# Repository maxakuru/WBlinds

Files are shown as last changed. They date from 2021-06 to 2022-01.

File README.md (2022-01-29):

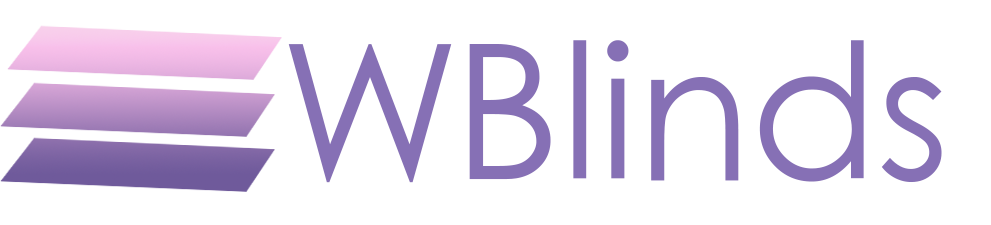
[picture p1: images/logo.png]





Build Wifi-connected smart blinds using ESP32 and off-the-shelf components for <$50.

🌟 Including...
* [HTTP/REST API](#http)
* [MQTT API](#mqtt) & client
* Native [Homekit](#homekit) integration
* Halts on home detection
* [Web UI](#web-ui) for controlling/configuring

## Table of Contents
<!--ts-->
   * [Setup](#setup)
      * [Hardware](#hardware)
      * [Circuit](#circuit)
      * [Software](#software)
   * [APIs](#apis)
   * [Web UI](#web-ui)
   * [Configuration](#configuration)
   * [Development](#development)
      * [Custom Integrations](#custom-integrations)
   * [Appendix](#appendix)
      * [Other Files](#other-files)
      * [Choosing a Motor](#choosing-a-motor)
<!--te-->

<h2 id="setup">✏️ Setup</h2>

### Hardware
These are some suggestions for hardware to use. The first link in each row is the product I used for the prototype. All links are non-affiliate and can be found elsewhere if you look around. Prices are estimates including shipping at the time I purchased and may have changed since then; I suggest searching around if so.

<table>
  <tbody>
    <tr>
      <th>Part ~~~~~~~~</th>
      <th>Purchase Links ~~~~~~~~~~~~~~~~~~~~~~~~~~~~</th>
      <th>Notes <br> ~~~~~~~~~~~~~~~~~~~~~~~~~~~~</th>
    </tr>
    <tr>
      <td>ESP32</td>
      <td>
        • <a href=https://www.aliexpress.com/item/1005001648850998.html>32S Devkit "V1" (AliExpress, $4)</a><br>
        • <a href=https://www.mouser.com/ProductDetail/Espressif-Systems/ESP32-S2-DevKitM-1?qs=DPoM0jnrROXzO8seOHN%252BOQ%3D%3D>32S Devkit M1 (Mouser, $8)</a><br>
        • <a href=https://www.amazon.com/HiLetgo-ESP-WROOM-32-Development-Microcontroller-Integrated/dp/B0718T232Z>NodeMCU-32 (Amazon, $11)</a>
      </td>
      <td>Circuit below wass using the first link. Pin assignments may vary between boards, often the same pins but more/less extra pins, or power pins are in different places. Be sure to check the pinout.</td>
    </tr>
    <tr>
      <td>Stepper Driver</td>
      <td>
        • <a href=https://www.aliexpress.com/item/1005001374747956.html>A4988 (AliExpress, $2)</a><br>
        • <a href=https://www.pololu.com/product/1182>A4988 (Polulu, $6)</a><br>
        • <a href=https://www.amazon.com/Aokin-StepStick-Stepper-Driver-Printer/dp/B07JV835SW>5x A4988 (Amazon, $8)</a>
      </td>
      <td>Other drivers would work too, currently only A4988 is tested (using <a href=https://github.com/gin66/FastAccelStepper>FastAccelStepper</a>). <br><br> Be sure to <a href=https://youtu.be/89BHS9hfSUk>set the current limit</a> before attaching your motor.</td>
    </tr>
    <tr>
      <td>Stepper Motor</td>
      <td>
        • <a href=https://www.aliexpress.com/item/1005002191787745.html>1.5A 45Ncm (AliExpress, $18)</a><br>
         <a href="https://www.omc-stepperonline.com/nema-17-bipolar-42ncm-59-49oz-in-1-5a-42x42x39mm-4-wires-w-1m-cable-and-connector.html">1.5A 42Ncm (StepperOnline, $5 at time of writing)</a>
        • <a href=https://www.pololu.com/product/2267>1.7A 36Ncm (Polulu, $18)</a><br>
        • <a href=https://www.amazon.com/Twotrees-Stepper-17HS4401-Connector-Printer/dp/B07THK76QQ>1.5A 42Ncm (Amazon, $10)</a>
      </td>
      <td>This may be over/underpowered for your needs, depending on the weight of the blinds. <br> <br> See <a href="#choosing-a-motor">choosing a motor</a>. <br> <br> 
      Note: The newest 3d designs use a worm gear with a 30:1 reductions so a much smaller motor will work, but the movement speed is greatly reduced with that design.</td>
    </tr>
    <tr>
      <td>3.3V Step-down Regulator</td>
      <td>
        • <a href=https://www.aliexpress.com/item/4000714041437.html>5-40V to 3.3V (AliExpress, $2)</a><br>
        • <a href=https://www.pololu.com/category/209/d24v5fx-step-down-voltage-regulators>D24V5Fx (Polulu, $5)</a><br>
        • <a href=https://www.amazon.com/Anmbest-AMS1117-3-3-4-75V-12V-Voltage-Regulator/dp/B07CP4P5XJ>10x 5-12V to 3.3v (Amazon, $9)</a>
      </td>
      <td>Circuit below is using the one from AliExpress.  Others may have different number of pins or pin orders, so check the pinout before wiring.</td>
    </tr>
    <tr>
      <td>Power supply</td>
      <td>
        • <a href=https://www.aliexpress.com/item/1005001555277278.html>24V 5A (AliExpress, $13)</a><br>
        • <a href=https://www.pololu.com/product/1468>12V 5A (Polulu, $19)</a><br>
        • <a href=https://www.amazon.com/Converter-100-220V-Transformer-5-5x2-1mm-Accessories/dp/B08C594VNP>12V 5A (Amazon, $10)</a>
      </td>
      <td>You can (and probably want to) use a voltage over the motor's rating.  That's fine, you just need to stay below it's rated current. <br> <br>  The current needed depends on motor rating and how many blinds you'll be moving simultaneously with the same power supply.</td>
    </tr>
    <tr>
      <td>DC barrel jack</td>
      <td>
        • <a href=https://www.aliexpress.com/item/4000215113209.html>5.5mm x 2.1mm (AliExpress, $3)</a><br>
      </td>
      <td></td>
    </tr>
    <tr>
      <td>Microswitch</td>
      <td>
        • <a href=https://www.aliexpress.com/item/1926553469.html>5x (AliExpress, $2)</a><br>
        • <a href=https://www.pololu.com/product/1402>1x (Polulu, $1)</a><br>
        • <a href=https://www.amazon.com/Antrader-KW4-3Z-3-Micro-Switch-Switches/dp/B07GDD9PJL>6x (Amazon, $6)</a>
      </td>
      <td>Optional, used as a limit switch for the "fully open" position.  Any switch could work here.</td>
    </tr>
    <tr>
      <td>Blinds</td>
      <td>
        • <a href="https://www.ikea.com/us/en/p/hoppvals-room-darkening-cellular-blind-gray-20386440">HOPPVALS (IKEA, $20-45)</a><br>
        • <a href="https://www.ikea.com/us/en/p/trippevals-black-out-cellular-blind-light-gray-00445006/">TRIPPEVALS (IKEA, $40-60)</a>
      </td>
      <td>My builds use cellular shades from IKEA, modified to wrap the cord around a 3D printed axis, instead of the retail spring mechanism. <br><br>  Any blinds that can be moved by wrapping a cord around an axis could easily be adapted.  Most cordless blinds could be used with some modifications. Roller blinds would be the easiest in most cases.</td>
    </tr>
  </tbody>
</table>

### Circuit
Schematic files are located in the `pcb/` directory. Currently there is a devkit that can be fabricated that fits header pins and will use the following components. Check the parts list carefully, only the first item in each section will fit, since they are what I ordered, but other parts may not. The gerber output is a 2 layer board created with [JLCPCB](https://jlcpcb.com/)'s CAM generator.
- 30 pin ESP32 devkit
- 3 pin buck converter (middle pin GND)
- 3 pin DC barrel jack

You'll also want some pin headers to solder on, both male and female. The parts are throughhole and the gerber has drill holes so you can skip them if you'd like, but I'd recommend at least making the A4988 removable in case you pop one.

#### Schematic
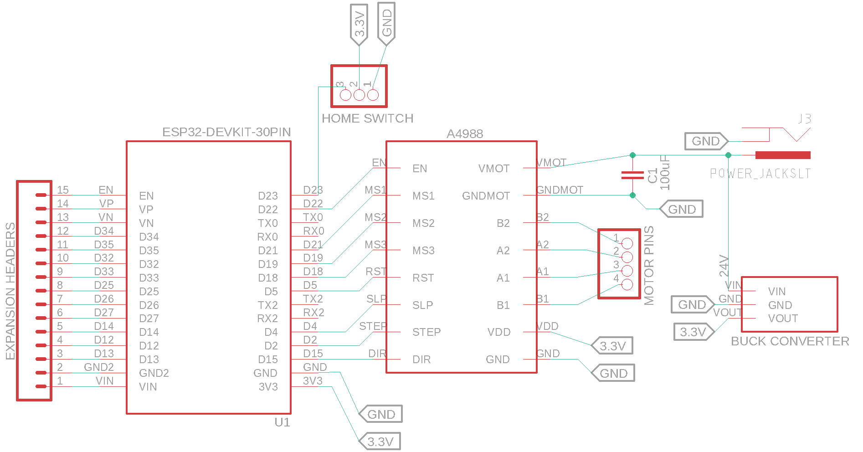
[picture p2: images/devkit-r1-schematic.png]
schematic


#### Devkit
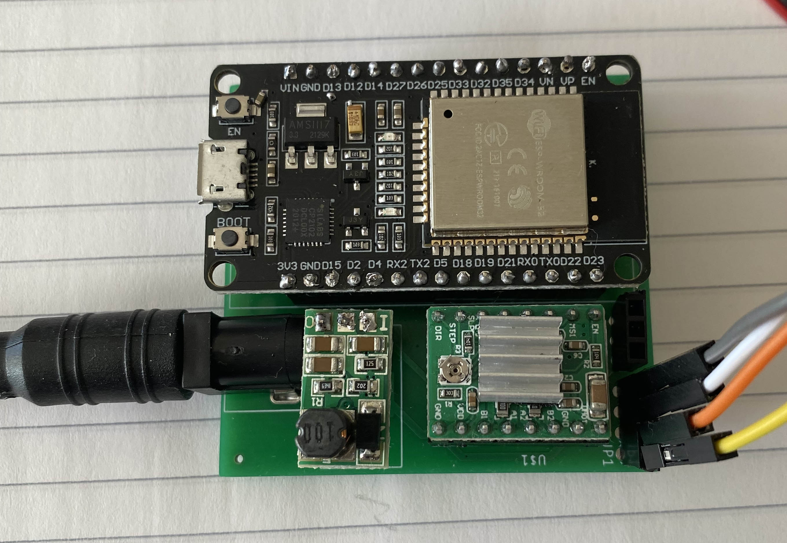
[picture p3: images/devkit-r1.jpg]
devkit


* **Remember to [adjust the current limit](https://youtu.be/89BHS9hfSUk) of the A4988 BEFORE connecting it to the circuit** -- keep the magic smoke inside.
* The pins can be set via the [web UI](#settings), feel free to use different ones.
* Be sure not to apply 12/24V to your ESP or `Vc` (or VDD) of the driver IC. It only goes to `Vm` to power the motor, everything else can use 3.3v.
* A4988's `RST` and `SLP` can be connected to each other if you don't care about the ability to sleep the motor.

### 3D Parts
Included in the `/3d` directory are 2 revisions of printable designs for WBlinds, crafted specifically for Ikea HOPPVALS. The same 2 mechanisms could be reworked for any other blinds. `r1` has the added benefit of a worm gear mechanism, so power doesn't need to be constantly applied to keep the blinds in place, even with heavy materials.

#### Revision 1
These are screenshots of the design to give you an idea of how parts fit together. It may be useful to put a damper ([Amazon](https://www.amazon.com/Rubber-Stepper-Vibration-Damper-Screws/dp/B07415B39B) | [AliExpress](https://www.aliexpress.com/item/4000058411445.html)) between the bracket and the stepper to cut down on vibration & noise.

**Default**

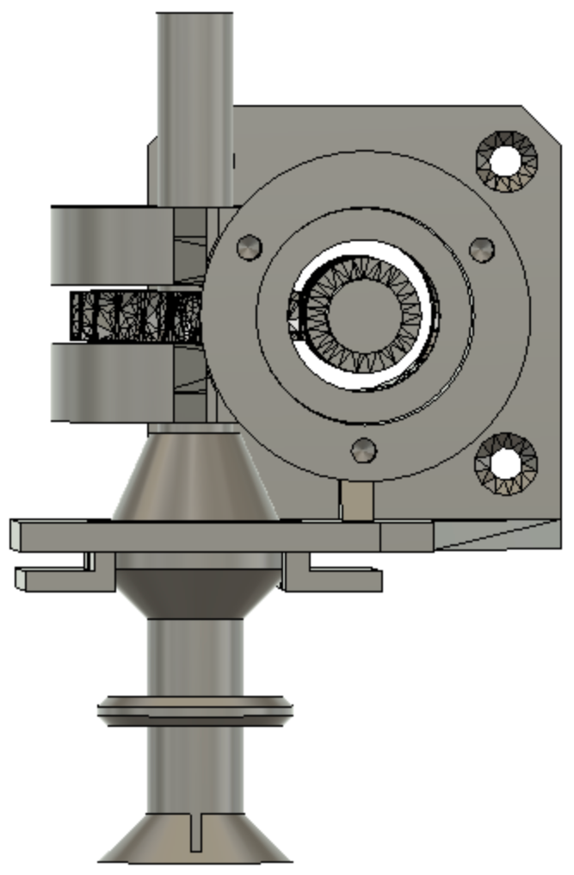
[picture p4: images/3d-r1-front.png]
r1-front
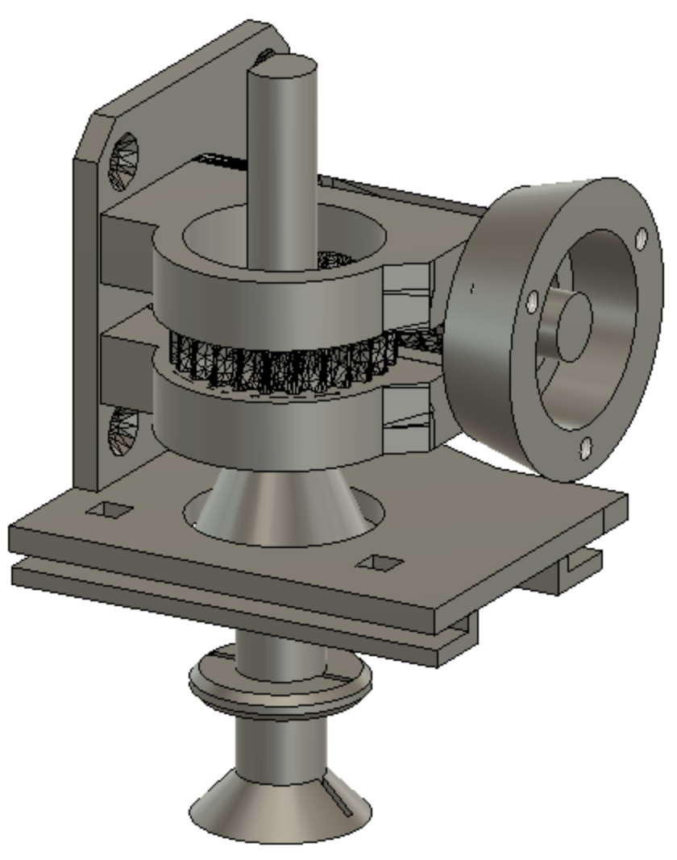
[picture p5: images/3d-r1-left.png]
r1-left
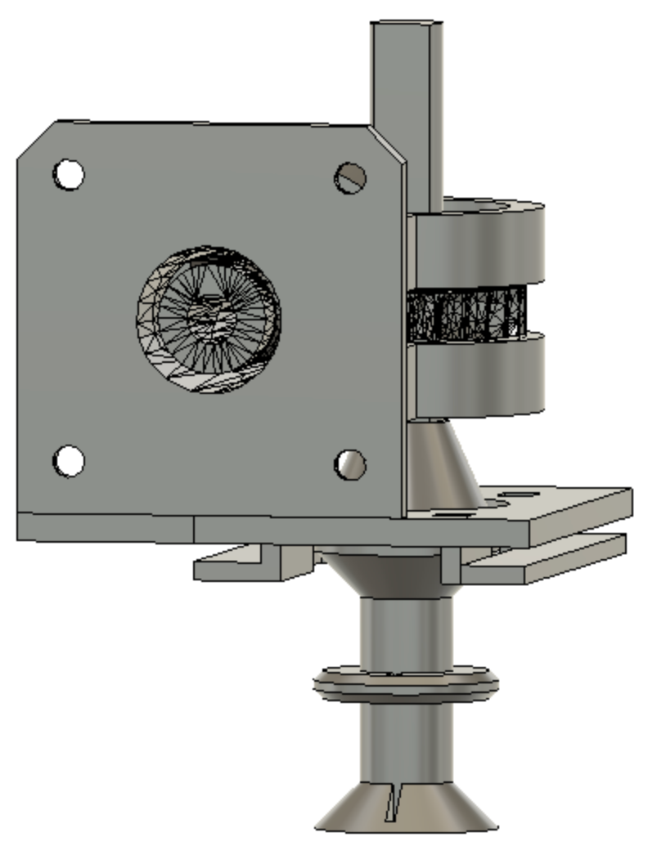
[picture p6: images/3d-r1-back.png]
r1-back
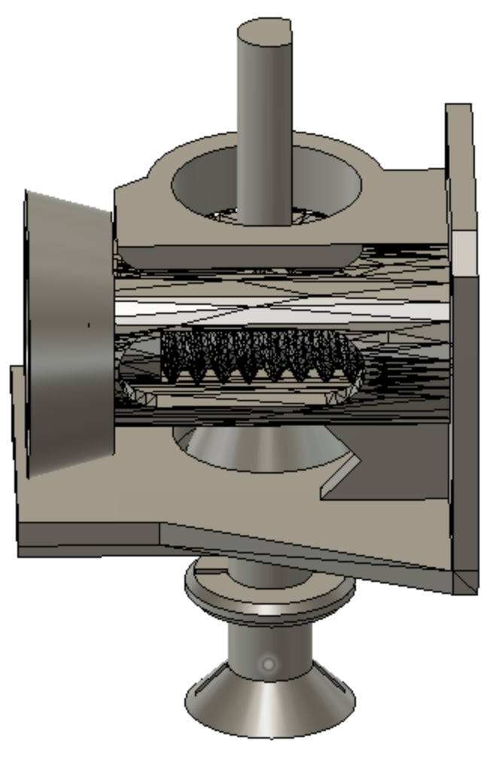
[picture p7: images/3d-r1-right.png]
r1-right


> The `3d/r1/cam/` contains an experimental (and not great) barrel cam mechanism to guide the string along an alternating path around the center spool, functionally similar to what a fishing reel does with a string guide. This can be sticky with 3D-printed parts, and with a good placement of `string-guide.stl`s, it isn't necessary to keep the spooling even.

**With optional cam exposed**

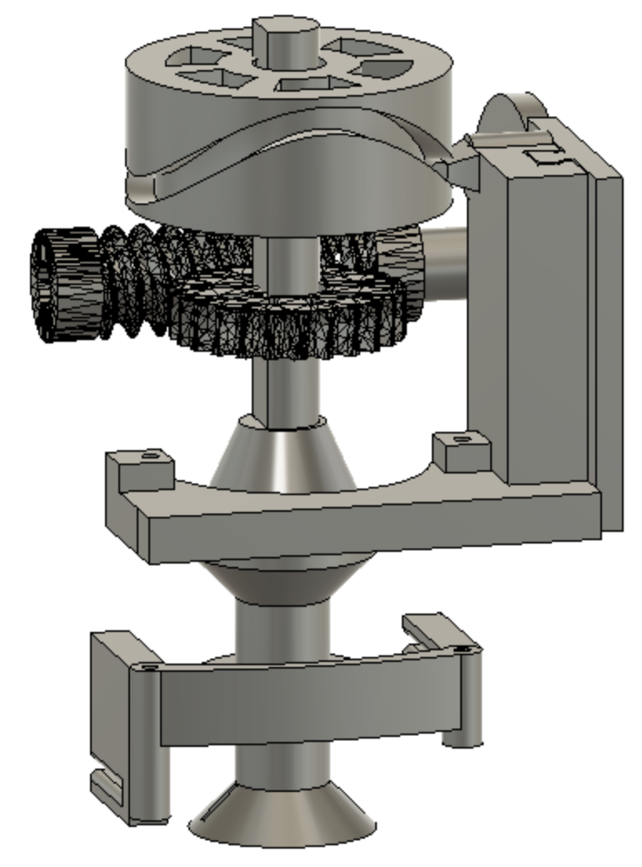
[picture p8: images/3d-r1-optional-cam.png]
r1-with-cam


### Software
1. Connect ESP32 to your computer via USB
2. `git clone https://github.com/maxakuru/WBlinds.git`
3. `cd WBlinds && yarn`
4. `yarn build:cpp`
5. `yarn flash`
6. On first boot an access point will be started, connect to it:
    * SSID: `WBlinds-XXXXXX`
    * Default password: `Wbl1nds-1337`
7. After connecting, a webpage should open to configure settings. If not, go to http://4.3.2.1/settings?tab=gen
8. Configure SSID, password, pins, etc. and tap "SAVE"
9. You will be disconnected from the AP. Find the IP address of the device on your network and enter it in your browser.
> Steps 3-5 assume you have PlatformIO, Node.js, and Yarn installed. You can also flash without Node/Yarn by using the [PlatformIO VSCode Plugin](#tools). You can also use the [scripts](#scripts) to do other stuff.

<h2 id="apis">🔌 APIs</h2>

These APIs are in flux!

### HTTP
```js
PUT <host:port>/api/state
// All fields optional
{ 
    "tPos": 50, //[0-100] (target position %, starts move)
    "pos": 50, // [0-100] (current position %)
    "accel": 99999, // [0-UINT32_MAX] (steps/s/s)
    "speed": 1000, // [0-something reasonable] (Hz)
}
```
```js
GET <host:port>/api/state
// 200
{ 
    "tPos": 50,
    "pos": 50,
    "accel": 99999,
    "speed": 1000
}
```

```js
POST <host:port> 
{ 
    "op": "up" | "down" | "stop" | "sleep"
}
```

```js
PUT <host:port>/api/settings
// All fields optional
// NOTE: data is sent in body as JSON. If that isn't acceptable for your use, set sensitive fields at compile time.
{ 
    gen: { 
        deviceName: "WBlinds", 
        mdnsName: "WBlinds", 
        emitSync: true,
        ssid: "My Network",
        pass: "supersecurepassword"
    },
    hw: {
        pStep: 19,
        pDir: 18,
        pEn: 23,
        pSleep: 21,
        pReset: 3,
        pMs1: 1,
        pMs2: 5,
        pMs3: 17,
        pHome: 4,
        cLen: 1650,
        cDia: 0.1,
        axDia: 15,
        stepsPerRev: 200,
        res: 16,
    },
    mqtt: {
        enabled: true,
        host: "192.168.1.99",
        port: 1883,
        topic: "WBlinds",
        user: "max",
        pass: "mysupersecurepassword"
    }
}
```
```js
GET <host:port>/api/settings
{ 
    gen: { 
        deviceName: "WBlinds", 
        mdnsName: "WBlinds",
        ssid: "Some SSID",
        mac: "abcdef123456",
        emitSync: true
    },
    hw: {
        pStep: 19,
        ...
        res: 16
    },
    mqtt: {
        enabled: true,
        host: "192.168.1.99",
        port: 1883,
        topic: "WBlinds",
        user: "max"
    }
}
```

```js
POST <host:port>/api/restore
// 202, ESP resets once completed
// This wipes Homekit config & state files
```

### MQTT
WBlinds subscribes to a wildcard based on the topic provided.
For example, a topic name `blinds/living_room` will subscribe to `blinds/living_room/#`.

The topic defines a number of actions without any payload, for example:
```sh
topic="blinds/living_room/up"
```
```sh
topic="blinds/living_room/down"
```
```sh
topic="blinds/living_room/stop"
```
```sh
topic="blinds/living_room/sleep"
```

Some topics can specify additional data:
```sh
topic="blinds/living_room/move"
body="{\"pos\":50,\"speed\":1000,\"accel\":1000}"
```
Where `pos` is %, `speed` is Hz, and `accel` is steps/s^2.

### Homekit
Native Homekit integration allows the ESP32 to be detected as a device without a bridge/emulator. This mode requires percentage-based position values, so it's important to calibrate the settings first.

The default Homekit pin is `111-22-333`, and it will be correctly identified as a "window covering".

<h2 id="web-ui">💻 Web UI</h2>

### Home
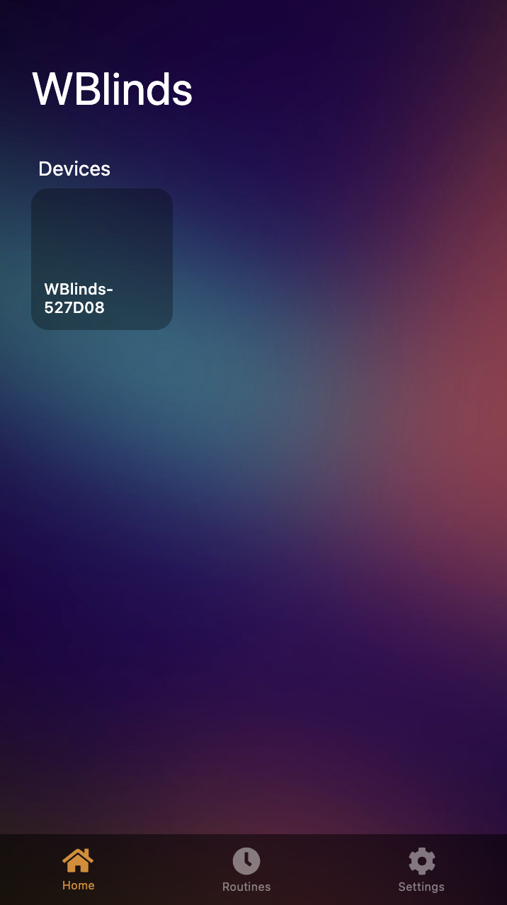
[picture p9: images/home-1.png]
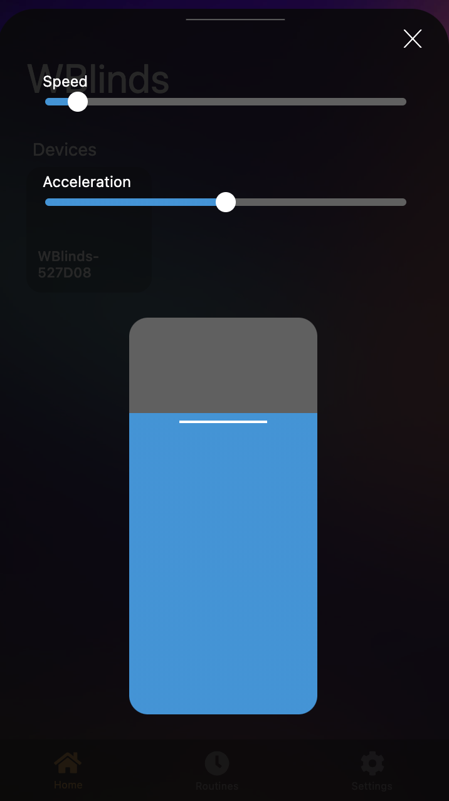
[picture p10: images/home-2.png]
 

### Settings
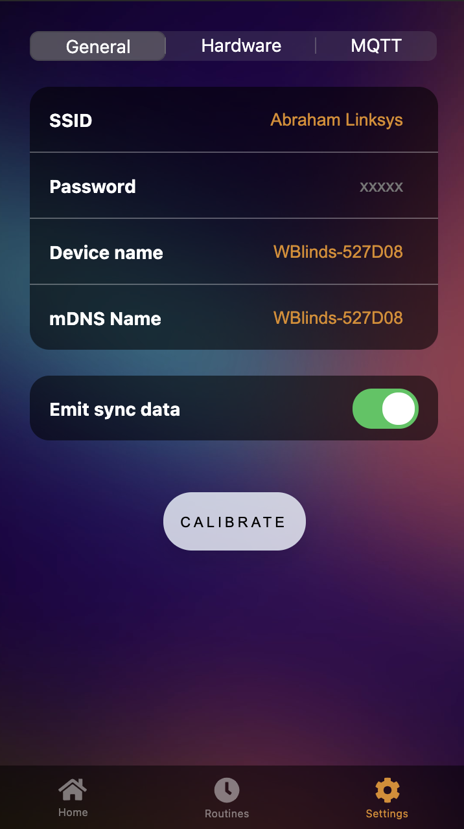
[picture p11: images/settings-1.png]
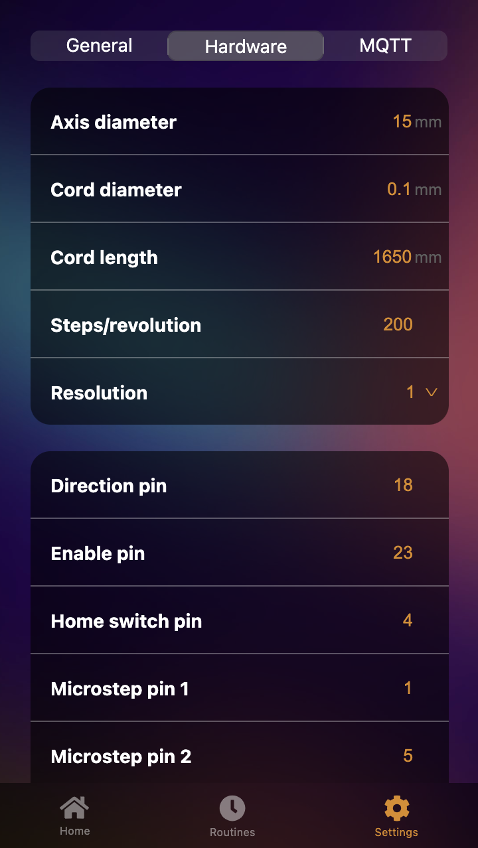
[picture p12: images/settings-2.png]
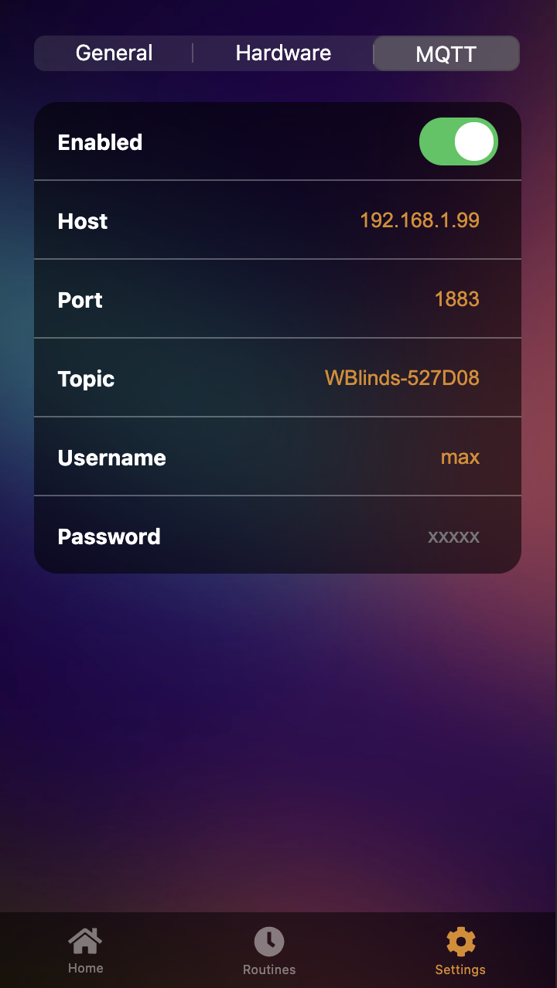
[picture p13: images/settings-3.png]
  

<h2 id="configuration">🔧 Configuration</h2>

There is a `Calibrate` button at `$HOST/settings?tab=gen` that will guide you through a 2 step calibration to find the correct bottom and top positions for the blinds on first setup. These settings will be persisted across power cycles and flashes of new firmwares, as long as you use the same partition.

### Default Pins
| Pin | Use | Description
| --- | --- | ---|
| `17`  | pDir | Controls direction (optional) |
| `5`  | pStep | Controls steps via PWM with A4988 (required) |
| `18`  | pSlp | Allows putting motor to sleep to save most power possible. (optional) |
| `23`  | pEn | Allows enabling/disabling motor with A4988. By default the motor is disabled and enabled between uses which lowers power consumption. (optional)
| `19` | pRst | Reset pin (optional)
| `1` | pMs1 | Microstep resolution pin 1, using microsteps can decrease sound (optional)
| `3` | pMs2 | Microstep resolution pin 2 (optional)
| `21` | pMs3 | Microstep resolution pin 3 (optional)
| `4` | pHomeSw | Home trigger switch, recommended as a way to hard stop when the blinds reach the fully contracted position to avoid damaging hardware when steps are skipped or malfunctions. (optional)

<h2 id="development">📝 Development</h2>

There are 2 projects that make up this repo: the C++ ESP controller and a TypeScript-based web UI. The web UI is transpiled to Javascript, inlined into HTML, then gzipped/chunked into header files with a script. All generated header files as well as transpiled JS is included in the repo, so no additional build steps are needed.

### Scripts
These can be run with `npm` or `yarn`, I'm currently using yarn. None of these are required to build and flash the ESP bin, as mentioned above all the files are checked into git, so you can compile the C part however you like.

However, these scripts are used for pre-commit hooks, so if you want to contribute you'll need Node.js.

#### UI
Build web UI in development/watch mode (outputs to `public/`):
```sh
yarn dev
```

Build web UI minified (outputs to `public/`, also runs `build:uih` afterwards):
```sh
yarn build:ui
```

Only generate header files from `public/`:
```sh
yarn build:uih
```

#### ESP
The following scripts depend on PlatformIO, and can be replaced with the toolbar quick actions in VSCode if you prefer.

Compile C++ (assumes *nix machine right now):
```sh
yarn build:cpp
```

Build & flash using pio:
```sh
yarn flash
```

Flash over-the-air (requires an initial flash while plugged in and WiFi connection established through settings):
```sh
yarn flash:ota $IP_OR_HOSTNAME
```

#### Both
You can combine all build scripts with:
```sh
yarn build
```

### Tools
I recommend using VSCode to build/flash. Eventually I plan to cut releases of precompiled binary that can be flashed directly, but for the time being you'll need to pull the code and compile it yourself. That is made very simple by the wonderful [PlatformIO](https://platformio.org/) - I highly recommend using it with their [VSCode plugin](https://platformio.org/install/ide?install=vscode).

There are some other suggested plugins in the `.vscode` directory; VSCode should suggest installing any missing plugin on first boot, but none are required.

### Custom integrations
Additional integrations can be built in by extending the `WBlindsObserver` class and attaching to it, specifying the event flags you are interested in.

```cpp
#include "defines.h"
#include "state.h"
#include "event.h"
#include <SpecialLib.h>

class SpecialLibIntegration : protected WBlindsObserver {
public:
    explicit SpecialLibIntegration() {
        EventFlags flags;
        flags.pos_ = true;
        flags.speed_ = true;
        flags.accel_ = true;
        flags.targetPos_ = true;
        // ... any other flags you're interested in
        State::getInstance()->Attach(this, flags);
    };
    ~SpecialLibIntegration() override {
        specialLib.teardown();
        State::getInstance()->Detach(this);
    };
    void SpecialLibIntegration::handleEvent(const WBlindsEvent& event) {
        // ... do something with the event
        auto state = State::getInstance();
        if(event.flags_.pos) {
            int pos = state.getPosition();
            specialLib.doStuffWithPosition(pos);
        }
     };
}
```

<h2 id="appendix">💤 Appendix</h2>

### Other files
The `/3d` directory contains some STL files that may be useful for building WBlinds. Those are designed for use with IKEA HOPPVALS, but would be close to the TRIPPVALS, too. There are 2 revisions:
1. `r0` uses a direct drive mechanism with a center axle along the entire width of the blind bracket. 
2. `r1` uses a worm gear and single spool in the center of the blinds bracket. This won't work with in window mounting.
> Note: Like everything else, those designs are a WIP :)

### Choosing a motor
TL;DR: [putting it together](#putting-it-together).

Out of the several variables a stepper motor has I've narrowed it down to the most important for our purposes. It's worth mentioning that WBlinds could be built using a regular DC motor and an encoder. Stepper motors are cheap and widely available, largely thanks to 3D printing. They also simplify the design quite a bit, so they're what I will focus on.

#### Skipped steps
A skipped step happens most often when:
1. The motor isn't provided with enough volts/amps to move the load.
2. The load is heavier than the stepper's holding torque.
3. Power is switched off, the motor is "released", and the load is greater than the motor's [detent torque](https://www.ierservices.com/blog/what-is-detent-torque).
3. Resonance/vibrations.

What skipped steps means to us is that the current state the motor "thinks" it's at is actually off by the number of steps skipped. This is especially bad if you don't have a limit switch to avoid damage, but also just annoying for the end user.

**#1 & #2** can be avoided by choosing a proper motor, power supply, and current limit for your stepper driver.

**#3** can be avoided by using a high gear ratio, a brake, or a homing switch and rehoming on reset.

**#4** is tricky to identify and to fix (you'll probably be fine ¯\\_(ツ)\_/¯ ).

#### Gear ratio
Not all stepper motors will have gears, but many do. Some also have a gearbox that increases the gear ratio. There are different kinds of gearboxes: [planetary](https://www.omc-stepperonline.com/ple-series-planetary-gearbox/ple-series-planetary-gearbox-gear-ratio-5-1-backlash-15-arc-min-for-nema-17-stepper-motor.html), [worm](https://www.aliexpress.com/item/32889194047.html), [spur](https://www.omc-stepperonline.com/pm-geared-stepper-motor/15x225mm-pm-stepper-motor-w-gear-ratio-1001-spur-gearbox). Then there are different [shapes](https://www.motioncontroltips.com/spur-gears-what-are-they-and-where-are-they-used/) of [gears](https://www.motioncontroltips.com/helical-gears-what-are-they-and-where-are-they-used/).. different [gear profiles](https://khkgears.net/new/gear_knowledge/abcs_of_gears-b/gear_tooth_profile.html).. different [tooth pitches](https://khkgears.net/new/gear_knowledge/abcs_of_gears-b/gear_accuracy.html) etc. 

For this guide we'll just think about **gear ratios and planetary stepper motors**.

Higher gear ratio benefits:
* Higher torque for less amperage
* Lower noise
* High holding torque (less drift when it's off)
* Fewer skipped steps (both from torque and resonance)

Drawbacks:
* Higher cost ($30+, or ~3-5x)
* Lower speed
* Often large or awkward shapes (for our purpose)

Considering our speed requirements are pretty low (or at least mine are), you could reasonably go with either. If you have large/heavy blinds it may make sense to look for a planetary stepper. I personally have been using regular NEMA17 steppers, but that's because I already had them.

> Note: There's also a [difference](https://blog.orientalmotor.com/stepper-motor-basics-pm-vs-vr-vs-hybrid) between permanent magnet (PM) planetary steppers and "hybrids".

> If you find a good, inexpensive planetary stepper to include in the parts list, contact me!

#### Speed/Torque
Whether you choose a regular stepper or gearbox stepper, the same final choices come up: how fast it moves vs. how much weight it can move.

As speed increases torque (generally) decreases, you can see this in the torque curves of a [regular stepper motor](https://ae01.alicdn.com/kf/HTB1WbFaTCzqK1RjSZFHq6z3CpXaq.jpg) and [planetary stepper](https://www.omc-stepperonline.com/download/11HS12-0674D-PG5_Torque_Curve.pdf). 

You want to find a motor that has a high enough speed that you aren't waiting until sunset for your blinds to open, and a high enough torque that you aren't skipping steps or stalling at 90% open. 

#### Putting it together
This won't be exact, but is a good enough estimate. I'll use the defaults from the included STLs and IKEA TRIPPEVALS, along with a constant speed. In practice, torque will be higher at the moment it starts to move, as acceleration is applied to go from stopped to max speed. I'll ignore it since the acceleration will be very low (as will top speed).

This is assuming a setup where a cord (A) or fabric (B) wraps around an axis that is directly driven by the motor.. something like these:

```
# A
|```````|   __________________
| Motor |==|__||||______||||__| <- cord spooled (ie. TRIPPEVALS)
|_______|  |   ||        ||   |
           |   ||        ||   |
           |___||________||___|

# B
|```````|   __________________
| Motor |==|__________________| <- roll of fabric (ie. roller blinds)
|_______|  |                  |
           |  Blocking window |
           |__________________|
```

1. Get some variables:
```
# constants
g = 9.8m/s^2

# The thicker the axis, the fewer rotations needed and faster it can move, at the cost of higher torque required.
Axis diameter   (Da) = 15mm = 1.5cm

# Thickness of cord or fabric, since Da increases as the cord is wrapped around.
Cord diameter   (Dc) = 0.5mm = 0.05cm

# Roughly length from top to bottom of window.
Cord Length     (Lc) = 1650m

# You can use a luggage scale to get a rough estimate, or just guesstimate conservatively.
Maximum load    (m)  = 5kg 

# Range of acceptable durations to go from fully opened to fully closed or vice versa. The faster it moves the louder it will be.
Slowest         (t-) = 3min
Fastest         (t+) = 1min
```

2. Calculate revolutions to fully wrapped:
> See handy calculator [here](https://www.giangrandi.ch/soft/spiral/spiral.shtml)
```ruby
         Dc - Da + sqrt[(Da - Dc)^2 + (4 * Dc * Lc) / pi]
Nrev = ------------------------------------------------
                      2 * Dc
```

```ruby
Nrev = (1 - 15 + sqrt((15 - 1)^2 + (4 * 0.5 * 1650) / 3.14)) / (2 * 0.5)
Nrev ~= 21
```

3. Calculate acceptable RPM range:
```ruby
RPM = Nrev / t
```
```ruby
RPM- = 21 / 3 = 7
RPM+ = 21 / 1 = 21
```

4. Calculate peak torque:
```ruby
# Some worst-case fudge here, in this example it barely impacts the result.
T = m * g * ((Nrev * Dc + Da) / 2)
```

```ruby
T = 5 * 9.8 * ((30 * 0.0005 + 0.0015) / 2)
T = 0.404 N.m ~= 40N.cm
```

So, a motor that can pull **40N.cm at around 7 to 21 RPM** is good for this example. Now you can browse motors and look at torque curves to find a suitable choice, like [this $10 stepper](https://www.aliexpress.com/item/1005002191787745.html?spm=a2g0s.9042311.0.0.27424c4dTeE5ku) ([torque curve](https://ae01.alicdn.com/kf/HTB1WbFaTCzqK1RjSZFHq6z3CpXaq.jpg)) or [this $24 planetary](https://www.omc-stepperonline.com/economy-planetary-gearbox/nema-14-stepper-motor-bipolar-l33mm-w-gear-raio-511-planetary-gearbox-14hs13-0804s-pg51.html) ([torque curve](https://www.omc-stepperonline.com/download/14HS13-0804S-PG51_Torque_Curve.pdf)).

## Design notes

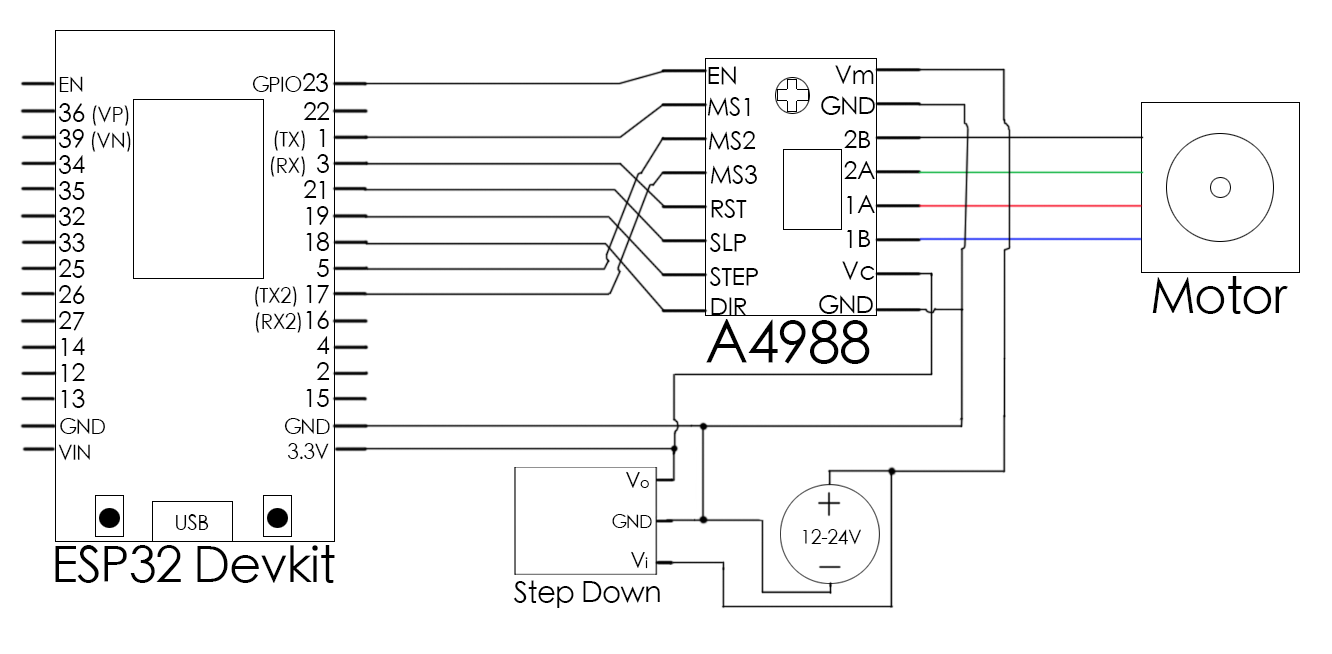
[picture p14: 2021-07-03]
images/circuit.png

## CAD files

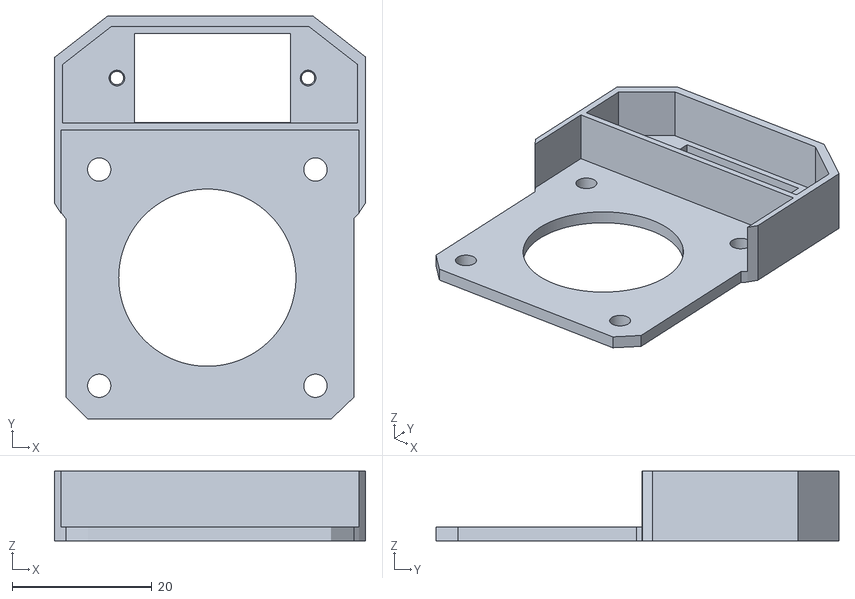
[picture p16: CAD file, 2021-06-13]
3d/r0/nema17-brake-mount-v6.stl
44.6 x 57.8 x 10.0

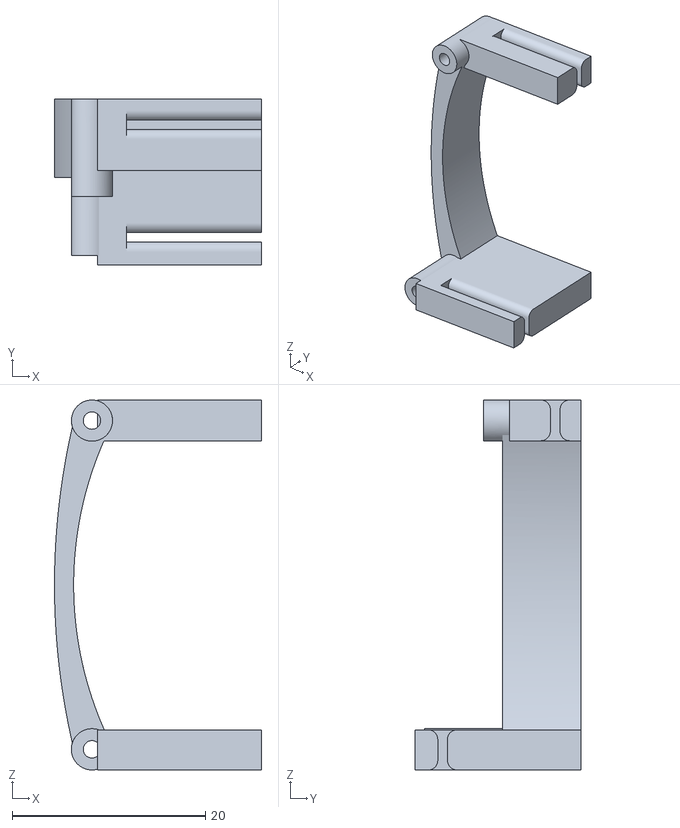
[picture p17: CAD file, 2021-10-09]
3d/r1/cam/guide-slip.stl
21.4 x 17.2 x 38.3

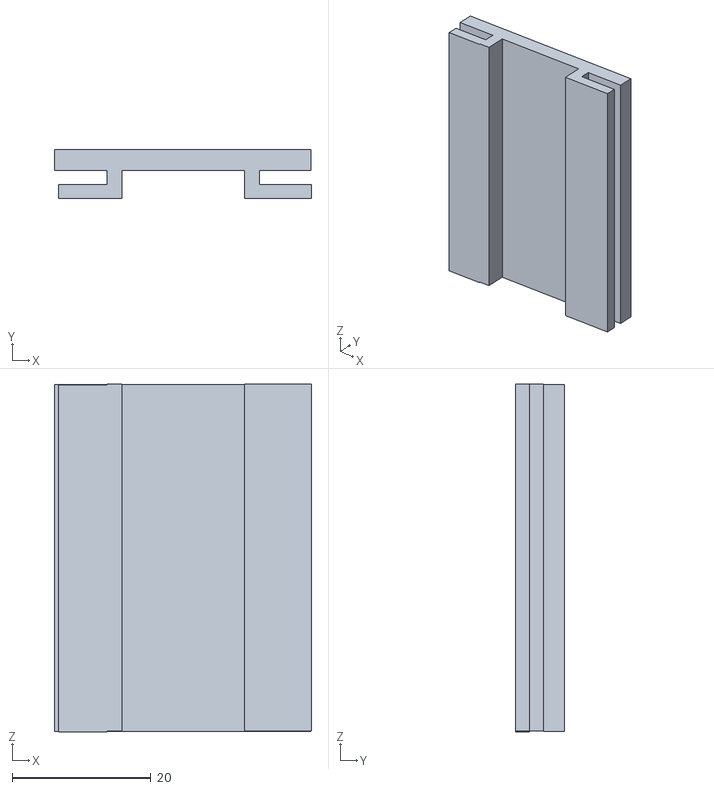
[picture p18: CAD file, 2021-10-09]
3d/r1/pcb-mount.stl
37.1 x 7.00 x 50.1

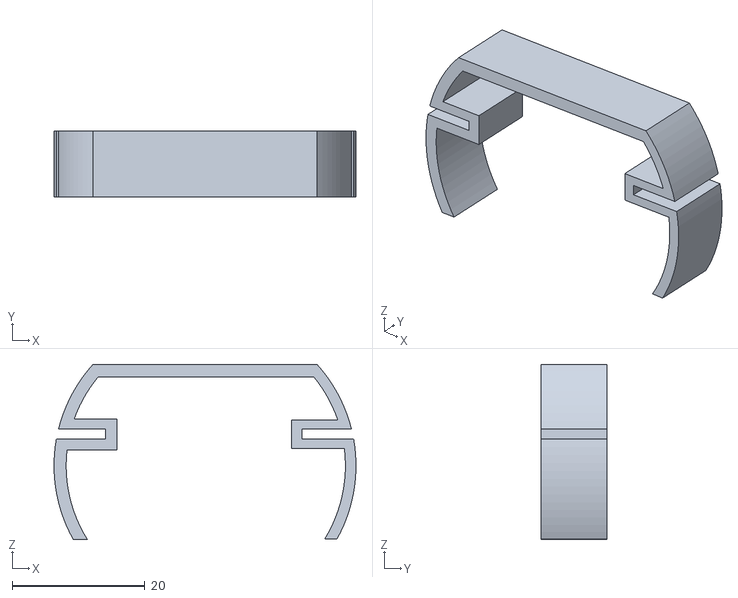
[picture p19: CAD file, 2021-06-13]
3d/r0/ikea-hoppvals-shell-v1.stl
45.5 x 10.0 x 26.4

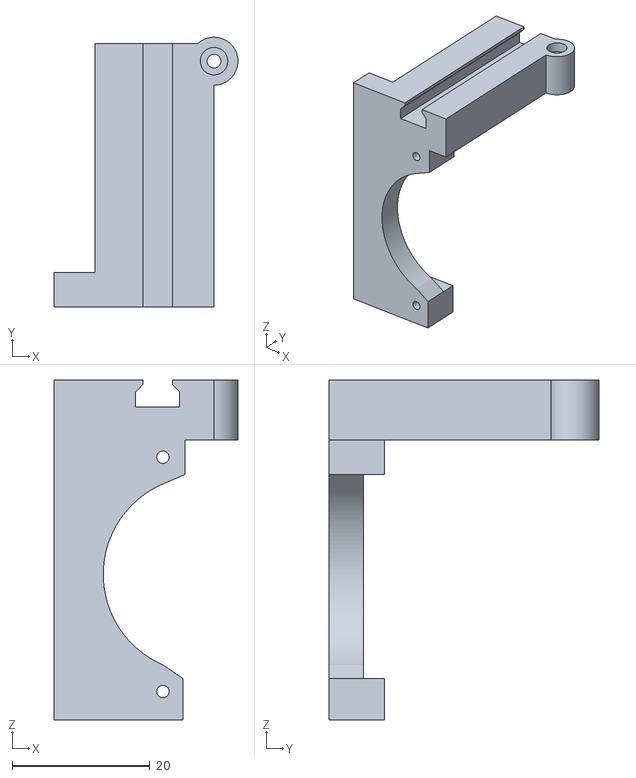
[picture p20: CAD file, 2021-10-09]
3d/r1/cam/groove-v5.stl
26.7 x 39.2 x 49.4

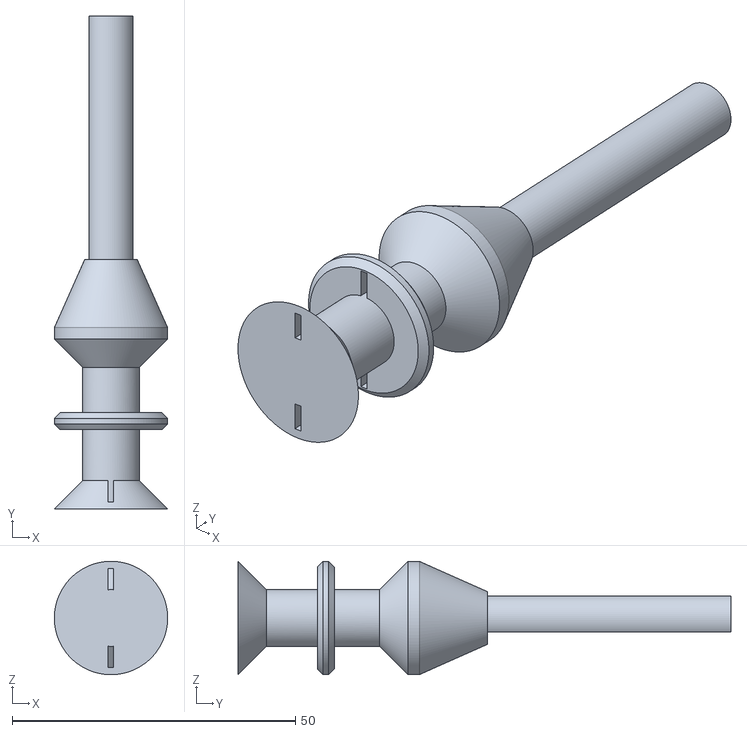
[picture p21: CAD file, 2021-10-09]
3d/r1/shaft-v3.stl
20.0 x 87.0 x 20.0

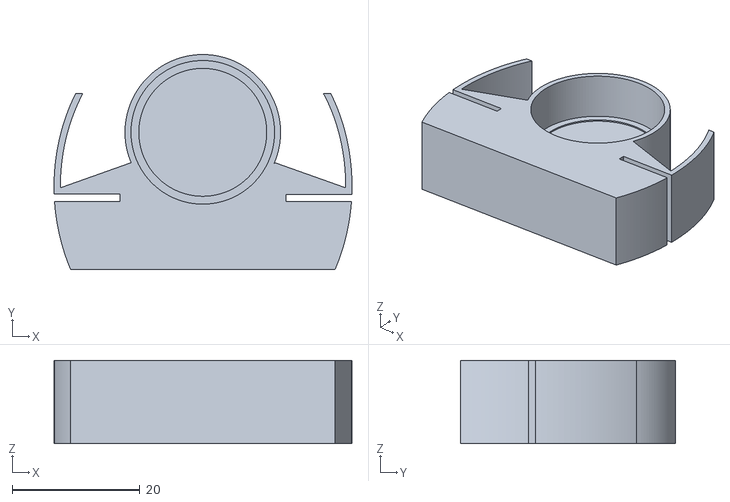
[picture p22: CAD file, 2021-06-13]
3d/r0/ikea-hoppvals-bearing-mount-v5.stl
46.6 x 33.6 x 13.0

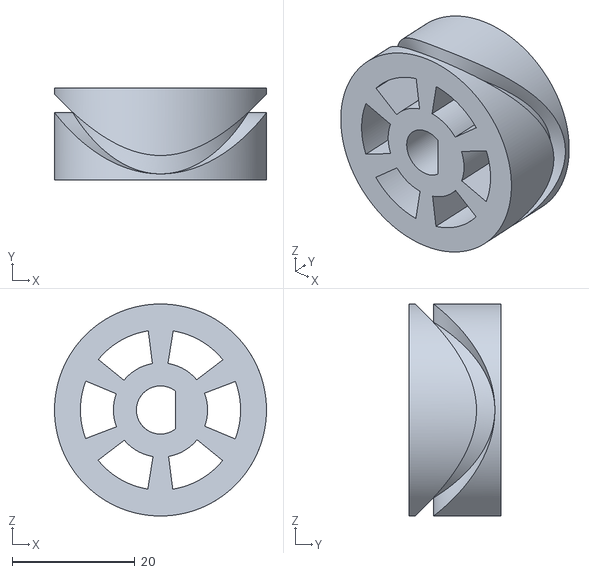
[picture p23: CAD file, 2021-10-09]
3d/r1/cam/cylinder.stl
34.6 x 15.0 x 34.6

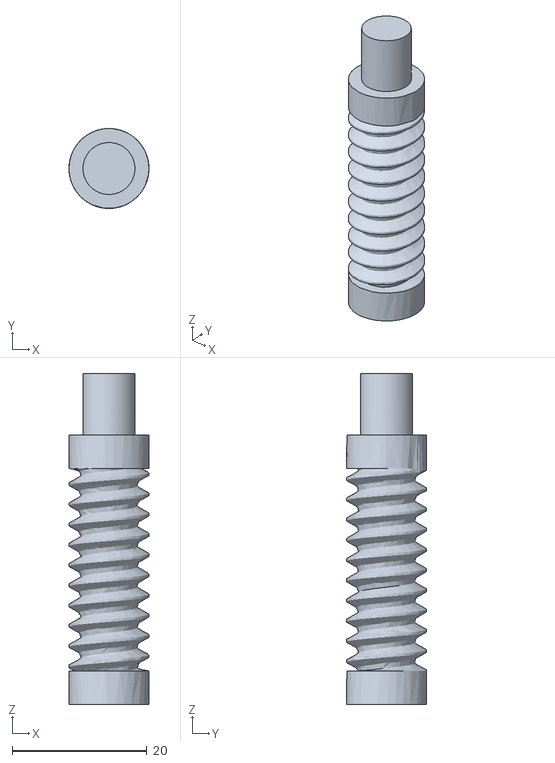
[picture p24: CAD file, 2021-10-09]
3d/r1/worm-v2.stl
11.9 x 11.9 x 49.1

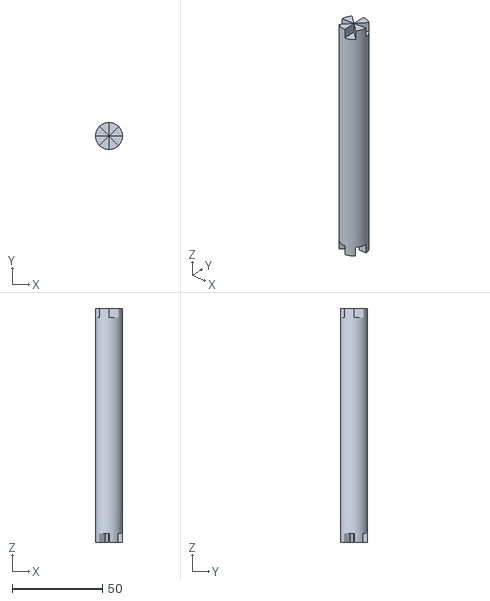
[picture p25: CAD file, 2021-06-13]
3d/r0/axis-segment-v3.stl
15.0 x 15.0 x 130.0

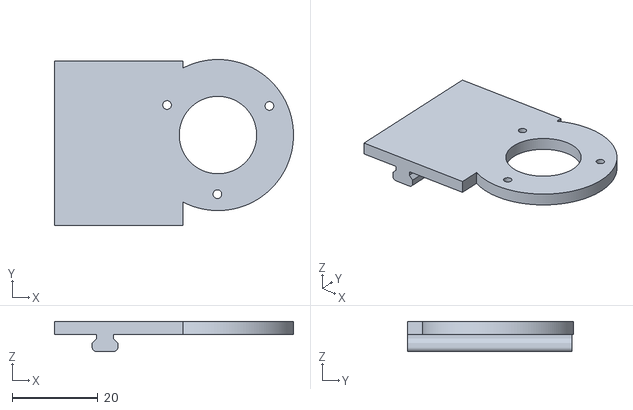
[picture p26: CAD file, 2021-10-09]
3d/r1/cam/guide.stl
55.7 x 38.7 x 7.00

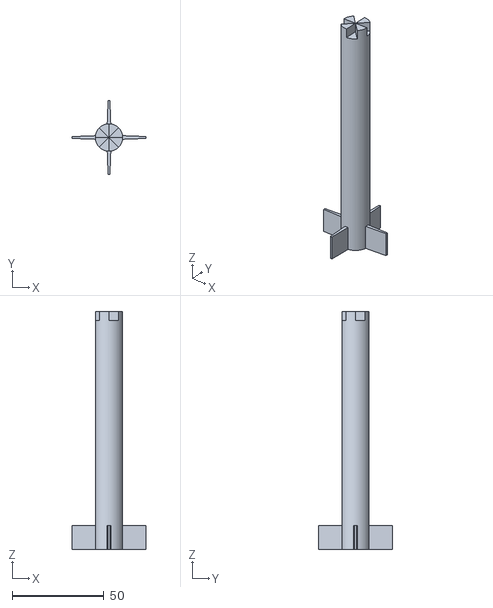
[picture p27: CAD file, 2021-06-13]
3d/r0/axis-v7.stl
40.5 x 40.5 x 130.0

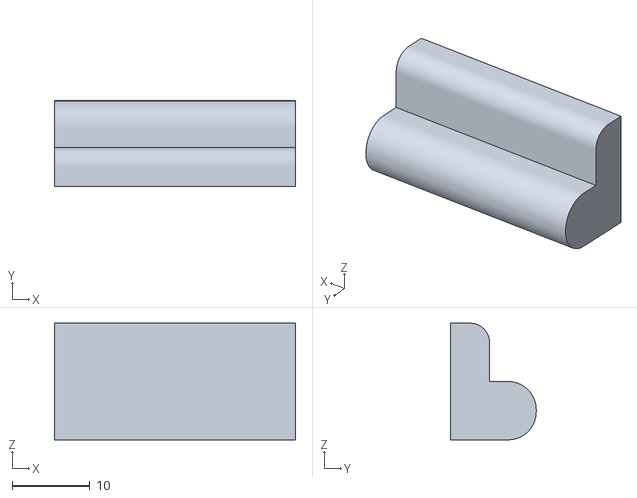
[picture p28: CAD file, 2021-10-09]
3d/r1/string-guide-v3.stl
31.0 x 11.0 x 15.0

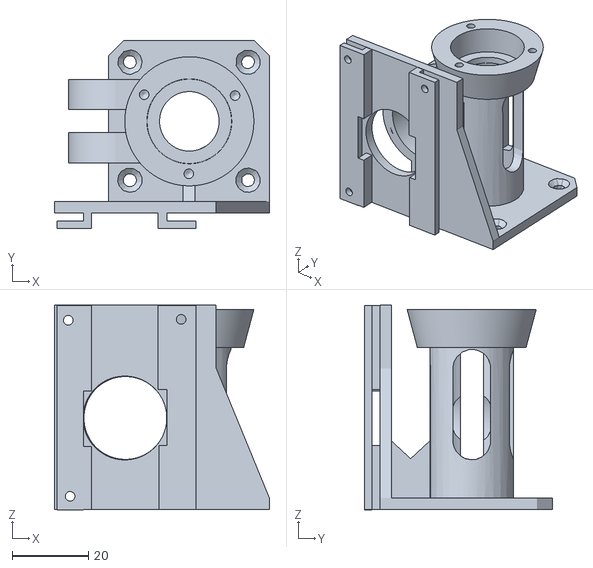
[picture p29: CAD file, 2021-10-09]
3d/r1/base-v5.stl
56.5 x 49.3 x 53.7

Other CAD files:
3d/r1/gear-v2.stl

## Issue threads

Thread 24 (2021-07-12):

CAD: Add stl for planetary gearbox

maxakuru, 2021-07-12:
- planetary gear reducer attachment for nema17 stepper
  - optional, reduce speed and increase torque without buying "real" planetaries
- gear reducer axis end mount
  - optional, just to add some holding torque/friction for regular steppers

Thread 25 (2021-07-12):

CAD: improve shaft, add spools

maxakuru, 2021-07-12:
- make spools to guide cords
- improve shaft/axis locking
- add axis end segment to work with gear reducer

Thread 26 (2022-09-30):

Build failing in VSCode with PlatformIO

xStatts, 2022-09-30:
Hi there,

This project is very impressive! What you've put together seems very powerful and easy to use, once the ESP32 is flashed. I'm very excited to have a go at putting this together, with the aim instead of having the stepper motor have a sprocket on it that turns the ball-cord for the roller blinds to be a bit more friendly to renters, whilst having HomeKit support!

However, I'm currently having some issues building the project in VSCode. First, I had to change the version number of the MQTT client to 0.9.0, as it seems that 0.8.2 doesn't exist any more. But now, when trying to build I get the following output, and my understanding of the dependencies/libraries here isn't deep enough to make a whole lot of sense. Any ides would be very appreciated! Apologies for console dump - happy to clean anything up if that makes it any easier.

` *  Executing task: platformio run

Processing esp32dev (platform: espressif32; board: esp32dev; framework: arduino)
------------------------------------------------------------------------------------------------------------------------------------------------------------
Verbose mode can be enabled via `-v, --verbose` option
CONFIGURATION: https://docs.platformio.org/page/boards/espressif32/esp32dev.html
PLATFORM: Espressif 32 (5.1.1) > Espressif ESP32 Dev Module
HARDWARE: ESP32 240MHz, 320KB RAM, 4MB Flash
DEBUG: Current (cmsis-dap) External (cmsis-dap, esp-bridge, esp-prog, iot-bus-jtag, jlink, minimodule, olimex-arm-usb-ocd, olimex-arm-usb-ocd-h, olimex-arm-usb-tiny-h, olimex-jtag-tiny, tumpa)
PACKAGES:
 - framework-arduinoespressif32 @ 3.20004.220825 (2.0.4)
 - tool-esptoolpy @ 1.30300.0 (3.3.0)
 - toolchain-xtensa-esp32 @ 8.4.0+2021r2-patch3
LDF: Library Dependency Finder -> https://bit.ly/configure-pio-ldf
LDF Modes: Finder ~ deep+, Compatibility ~ soft
Found 39 compatible libraries
Scanning dependencies...
Dependency Graph
|-- FastAccelStepper @ 0.23.5
|-- ArduinoJson @ 6.19.4
|-- AsyncTCP @ 1.1.1
|-- LittleFS_esp32 @ 1.0.6+sha.f0817ca
|   |-- FS @ 2.0.0
|-- ESP Async WebServer @ 1.2.3
|   |-- AsyncTCP @ 1.1.1
|   |-- FS @ 2.0.0
|   |-- WiFi @ 2.0.0
|-- AsyncMqttClient @ 0.9.0+sha.89bf464
|   |-- AsyncTCP @ 1.1.1
|-- FS @ 2.0.0
|-- WiFi @ 2.0.0
|-- homekit
|-- DNSServer @ 2.0.0
|   |-- WiFi @ 2.0.0
|-- ArduinoOTA @ 2.0.0
|   |-- WiFi @ 2.0.0
|   |-- Update @ 2.0.0
|   |-- ESPmDNS @ 2.0.0
|   |   |-- WiFi @ 2.0.0
|-- Update @ 2.0.0
Building in release mode
Compiling .pio/build/esp32dev/libaaf/FastAccelStepper/StepperISR_esp32.cpp.o
<command-line>: warning: ISO C++11 requires whitespace after the macro name
Compiling .pio/build/esp32dev/lib3fe/LittleFS_esp32/LITTLEFS.cpp.o
<command-line>: warning: ISO C++11 requires whitespace after the macro name
.pio/libdeps/esp32dev/FastAccelStepper/src/StepperISR_esp32.cpp: In function 'void apply_command(StepperQueue*, const queue_entry*)':
.pio/libdeps/esp32dev/FastAccelStepper/src/StepperISR_esp32.cpp:110:27: error: 'volatile struct mcpwm_timer_regs_t' has no member named 'status'; did you mean 'timer_status'?
   if (mcpwm->timer[timer].status.value <= 1) {  // mcpwm Timer is stopped ?
                           ^~~~~~
                           timer_status
.pio/libdeps/esp32dev/FastAccelStepper/src/StepperISR_esp32.cpp:111:25: error: 'volatile struct mcpwm_timer_regs_t' has no member named 'period'
     mcpwm->timer[timer].period.upmethod = 0;    // 0 = immediate update, 1 = TEZ
                         ^~~~~~
.pio/libdeps/esp32dev/FastAccelStepper/src/StepperISR_esp32.cpp:113:25: error: 'volatile struct mcpwm_timer_regs_t' has no member named 'period'
     mcpwm->timer[timer].period.upmethod = 1;  // 0 = immediate update, 1 = TEZ
                         ^~~~~~
.pio/libdeps/esp32dev/FastAccelStepper/src/StepperISR_esp32.cpp:115:23: error: 'volatile struct mcpwm_timer_regs_t' has no member named 'period'
   mcpwm->timer[timer].period.period = ticks;
                       ^~~~~~
.pio/libdeps/esp32dev/FastAccelStepper/src/StepperISR_esp32.cpp:118:12: error: 'struct mcpwm_dev_t' has no member named 'channel'
     mcpwm->channel[timer].generator[0].utea = 1;
            ^~~~~~~
.pio/libdeps/esp32dev/FastAccelStepper/src/StepperISR_esp32.cpp:170:12: error: 'struct mcpwm_dev_t' has no member named 'channel'
     mcpwm->channel[timer].generator[0].utea = 2;
            ^~~~~~~
.pio/libdeps/esp32dev/FastAccelStepper/src/StepperISR_esp32.cpp: In function 'void init_stop(StepperQueue*)':
.pio/libdeps/esp32dev/FastAccelStepper/src/StepperISR_esp32.cpp:182:23: error: 'volatile struct mcpwm_timer_regs_t' has no member named 'mode'
   mcpwm->timer[timer].mode.start = 0;  // 0: stop at TEZ
                       ^~~~
.pio/libdeps/esp32dev/FastAccelStepper/src/StepperISR_esp32.cpp: In function 'void mcpwm0_isr_service(void*)':
.pio/libdeps/esp32dev/FastAccelStepper/src/StepperISR_esp32.cpp:223:20: error: 'volatile union mcpwm_int_st_reg_t' has no member named 'cmpr0_tea_int_st'
   if (mcpwm.int_st.cmpr##TIMER##_tea_int_st != 0) {   \
                    ^~~~
.pio/libdeps/esp32dev/FastAccelStepper/src/StepperISR_esp32.cpp:233:3: note: in expansion of macro 'MCPWM_SERVICE'
   MCPWM_SERVICE(MCPWM0, 0, 0);
   ^~~~~~~~~~~~~
.pio/libdeps/esp32dev/FastAccelStepper/src/StepperISR_esp32.cpp:223:20: error: 'volatile union mcpwm_int_st_reg_t' has no member named 'cmpr1_tea_int_st'
   if (mcpwm.int_st.cmpr##TIMER##_tea_int_st != 0) {   \
                    ^~~~
.pio/libdeps/esp32dev/FastAccelStepper/src/StepperISR_esp32.cpp:234:3: note: in expansion of macro 'MCPWM_SERVICE'
   MCPWM_SERVICE(MCPWM0, 1, 1);
   ^~~~~~~~~~~~~
.pio/libdeps/esp32dev/FastAccelStepper/src/StepperISR_esp32.cpp:223:20: error: 'volatile union mcpwm_int_st_reg_t' has no member named 'cmpr2_tea_int_st'
   if (mcpwm.int_st.cmpr##TIMER##_tea_int_st != 0) {   \
                    ^~~~
.pio/libdeps/esp32dev/FastAccelStepper/src/StepperISR_esp32.cpp:235:3: note: in expansion of macro 'MCPWM_SERVICE'
   MCPWM_SERVICE(MCPWM0, 2, 2);
   ^~~~~~~~~~~~~
.pio/libdeps/esp32dev/FastAccelStepper/src/StepperISR_esp32.cpp: In function 'void mcpwm1_isr_service(void*)':
.pio/libdeps/esp32dev/FastAccelStepper/src/StepperISR_esp32.cpp:223:20: error: 'volatile union mcpwm_int_st_reg_t' has no member named 'cmpr0_tea_int_st'
   if (mcpwm.int_st.cmpr##TIMER##_tea_int_st != 0) {   \
                    ^~~~
.pio/libdeps/esp32dev/FastAccelStepper/src/StepperISR_esp32.cpp:238:3: note: in expansion of macro 'MCPWM_SERVICE'
   MCPWM_SERVICE(MCPWM1, 0, 3);
   ^~~~~~~~~~~~~
.pio/libdeps/esp32dev/FastAccelStepper/src/StepperISR_esp32.cpp:223:20: error: 'volatile union mcpwm_int_st_reg_t' has no member named 'cmpr1_tea_int_st'
   if (mcpwm.int_st.cmpr##TIMER##_tea_int_st != 0) {   \
                    ^~~~
.pio/libdeps/esp32dev/FastAccelStepper/src/StepperISR_esp32.cpp:239:3: note: in expansion of macro 'MCPWM_SERVICE'
   MCPWM_SERVICE(MCPWM1, 1, 4);
   ^~~~~~~~~~~~~
.pio/libdeps/esp32dev/FastAccelStepper/src/StepperISR_esp32.cpp:223:20: error: 'volatile union mcpwm_int_st_reg_t' has no member named 'cmpr2_tea_int_st'
   if (mcpwm.int_st.cmpr##TIMER##_tea_int_st != 0) {   \
                    ^~~~
.pio/libdeps/esp32dev/FastAccelStepper/src/StepperISR_esp32.cpp:240:3: note: in expansion of macro 'MCPWM_SERVICE'
   MCPWM_SERVICE(MCPWM1, 2, 5);
   ^~~~~~~~~~~~~
.pio/libdeps/esp32dev/FastAccelStepper/src/StepperISR_esp32.cpp: In member function 'void StepperQueue::init(uint8_t, uint8_t)':
.pio/libdeps/esp32dev/FastAccelStepper/src/StepperISR_esp32.cpp:288:55: error: 'PERIPH_PWM0_MODULE' was not declared in this scope
     periph_module_enable(mcpwm_unit == MCPWM_UNIT_0 ? PERIPH_PWM0_MODULE
                                                       ^~~~~~~~~~~~~~~~~~
.pio/libdeps/esp32dev/FastAccelStepper/src/StepperISR_esp32.cpp:288:55: note: suggested alternative: 'PERIPHS_IO_MUX_MTDO_U'
     periph_module_enable(mcpwm_unit == MCPWM_UNIT_0 ? PERIPH_PWM0_MODULE
                                                       ^~~~~~~~~~~~~~~~~~
                                                       PERIPHS_IO_MUX_MTDO_U
.pio/libdeps/esp32dev/FastAccelStepper/src/StepperISR_esp32.cpp:289:55: error: 'PERIPH_PWM1_MODULE' was not declared in this scope
                                                     : PERIPH_PWM1_MODULE);
                                                       ^~~~~~~~~~~~~~~~~~
.pio/libdeps/esp32dev/FastAccelStepper/src/StepperISR_esp32.cpp:289:55: note: suggested alternative: 'PERIPHS_IO_MUX_MTDO_U'
                                                     : PERIPH_PWM1_MODULE);
                                                       ^~~~~~~~~~~~~~~~~~
                                                       PERIPHS_IO_MUX_MTDO_U
.pio/libdeps/esp32dev/FastAccelStepper/src/StepperISR_esp32.cpp:288:5: error: 'periph_module_enable' was not declared in this scope
     periph_module_enable(mcpwm_unit == MCPWM_UNIT_0 ? PERIPH_PWM0_MODULE
     ^~~~~~~~~~~~~~~~~~~~
Compiling .pio/build/esp32dev/libfc2/WiFi/WiFiClient.cpp.o
.pio/libdeps/esp32dev/FastAccelStepper/src/StepperISR_esp32.cpp:288:5: note: suggested alternative: 'esp_intr_enable'
     periph_module_enable(mcpwm_unit == MCPWM_UNIT_0 ? PERIPH_PWM0_MODULE
     ^~~~~~~~~~~~~~~~~~~~
     esp_intr_enable
.pio/libdeps/esp32dev/FastAccelStepper/src/StepperISR_esp32.cpp:297:20: error: 'volatile union mcpwm_clk_cfg_reg_t' has no member named 'prescale'
     mcpwm->clk_cfg.prescale = 5 - 1;
                    ^~~~~~~~
.pio/libdeps/esp32dev/FastAccelStepper/src/StepperISR_esp32.cpp:299:12: error: 'struct mcpwm_dev_t' has no member named 'timer_sel'; did you mean 'timer'?
     mcpwm->timer_sel.operator0_sel = 0;  // timer 0 is input for operator 0
            ^~~~~~~~~
            timer
.pio/libdeps/esp32dev/FastAccelStepper/src/StepperISR_esp32.cpp:300:12: error: 'struct mcpwm_dev_t' has no member named 'timer_sel'; did you mean 'timer'?
     mcpwm->timer_sel.operator1_sel = 1;  // timer 1 is input for operator 1
            ^~~~~~~~~
            timer
.pio/libdeps/esp32dev/FastAccelStepper/src/StepperISR_esp32.cpp:301:12: error: 'struct mcpwm_dev_t' has no member named 'timer_sel'; did you mean 'timer'?
     mcpwm->timer_sel.operator2_sel = 2;  // timer 2 is input for operator 2
            ^~~~~~~~~
            timer
.pio/libdeps/esp32dev/FastAccelStepper/src/StepperISR_esp32.cpp:303:23: error: 'volatile struct mcpwm_timer_regs_t' has no member named 'period'
   mcpwm->timer[timer].period.upmethod = 1;  // 0 = immediate update, 1 = TEZ
                       ^~~~~~
.pio/libdeps/esp32dev/FastAccelStepper/src/StepperISR_esp32.cpp:304:23: error: 'volatile struct mcpwm_timer_regs_t' has no member named 'period'
   mcpwm->timer[timer].period.prescale = TIMER_PRESCALER;
                       ^~~~~~
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
maxakuru, 2022-10-12:
Hey @xStatts - glad something looks helpful here!

Could you try replacing [lib_deps](https://github.com/maxakuru/WBlinds/blob/main/platformio.ini#L53) with pinned versions to start?

```
lib_deps =
	gin66/FastAccelStepper@0.23.2
	bblanchon/ArduinoJson@6.18.0
	me-no-dev/AsyncTCP@1.0.3
	https://github.com/lorol/LITTLEFS.git
	me-no-dev/ESP Async WebServer@1.2.3
	https://github.com/marvinroger/async-mqtt-client.git @0.9.0
```

I'll have the machine with my previous build next week, I can check what versions I had pinned then & see how upgrading goes

xStatts, 2022-11-03:
Thanks for your response! Apologies for the delay - have had a big house move.

Pinning lib_deps with those versions unfortunately gives the same output as before for me, where many errors are found within the FastAccelStepper src still, failing the build. Using different versions of FastAccelStepper released at around the same time gives some differing errors which is interesting, but never builds successfully. Let me know if I can send through any more info to assist!

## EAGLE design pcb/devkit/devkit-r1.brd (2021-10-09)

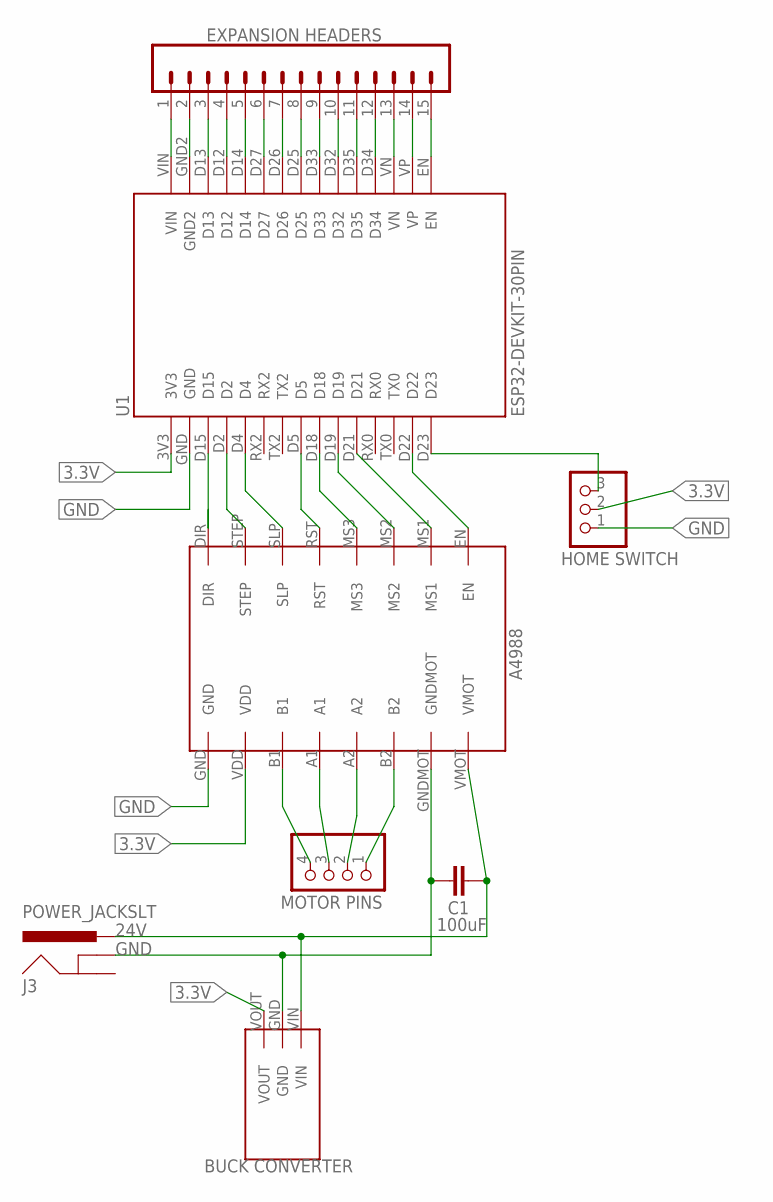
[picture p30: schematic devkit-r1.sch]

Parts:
BUCK: BUCK-CONVERTERBUCK-CONVERTER; BUCK-CONVERTER
C1: C2,5-3; C2.5-3
J1: CONN_15; 1X15
J3: POWER_JACKSLT; POWER_JACK_SLOT
JP1: PINHD-1X4; 1X04
JP2: PINHD-1X3; 1X03
U1: ESP32-DEVKIT-30PIN
U$1: A4988A4988; A4988

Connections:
3.3V: BUCK.VOUT, JP2.2, U1.3V3, U$1.VDD
24V: BUCK.VIN, C1.2, J3.PWR, U$1.VMOT
GND: BUCK.GND, C1.1, J3.GND@1 (GNDBREAK), JP2.1, U1.GND, U$1.GND, U$1.GNDMOT
unnamed: JP2.3, U1.D23
unnamed: U1.D22, U$1.EN
unnamed: JP1.4, U$1.B1
unnamed: JP1.3, U$1.A1
unnamed: JP1.2, U$1.A2
unnamed: JP1.1, U$1.B2
unnamed: U1.D21, U$1.MS1
unnamed: U1.D19, U$1.MS2
unnamed: U1.D18, U$1.MS3
unnamed: U1.D5, U$1.RST
unnamed: U1.D4, U$1.SLP
unnamed: U1.D2, U$1.STEP
unnamed: U1.D15, U$1.DIR
unnamed: J1.1, U1.VIN
unnamed: J1.2, U1.GND2
unnamed: J1.3, U1.D13
unnamed: J1.4, U1.D12
unnamed: J1.5, U1.D14
unnamed: J1.6, U1.D27
unnamed: J1.7, U1.D26
unnamed: J1.8, U1.D25
unnamed: J1.9, U1.D33
unnamed: J1.10, U1.D32
unnamed: J1.11, U1.D35
unnamed: J1.12, U1.D34
unnamed: J1.13, U1.VN
unnamed: J1.14, U1.VP
unnamed: J1.15, U1.EN
TX0: U1.TX0

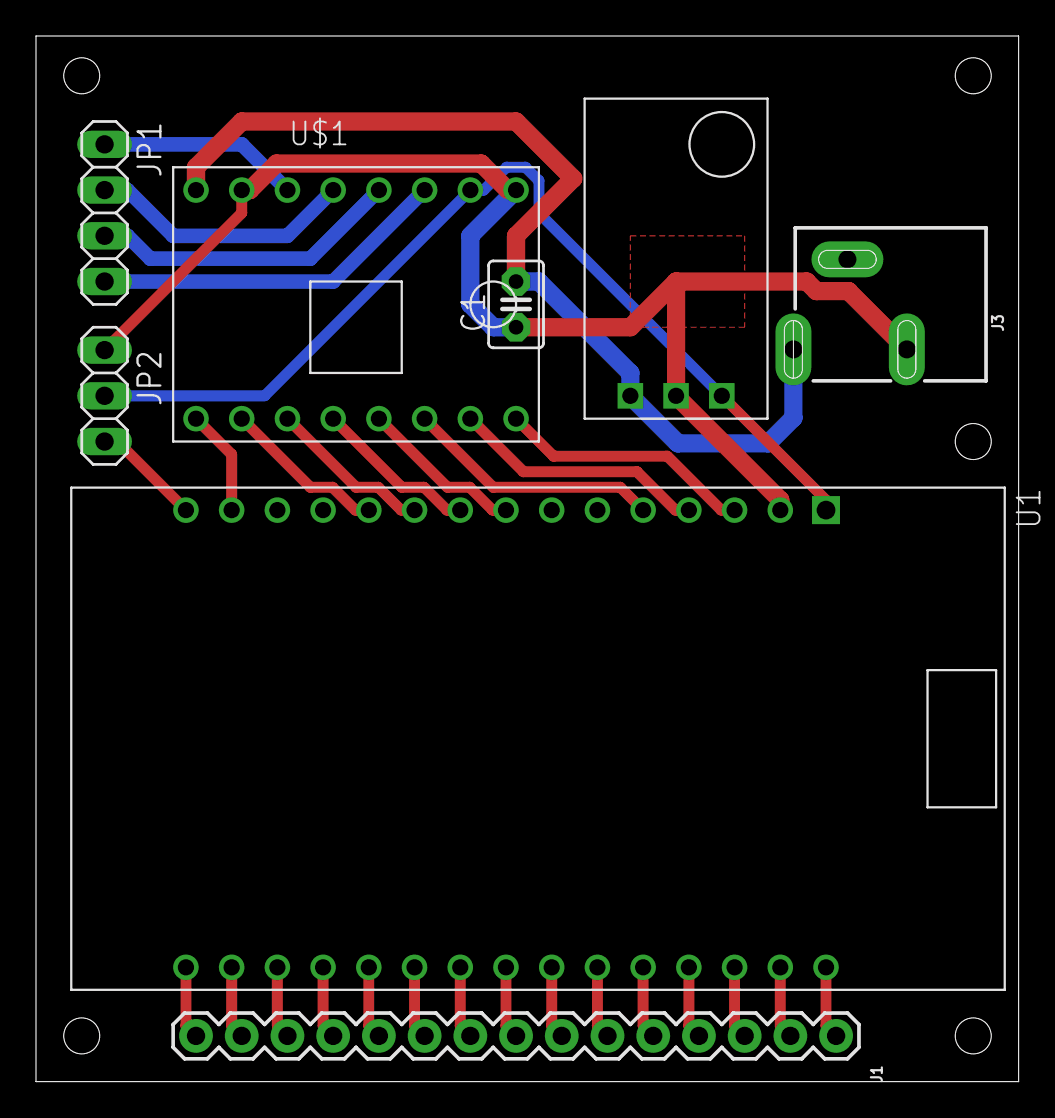
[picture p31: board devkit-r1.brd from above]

Board: 2 copper layers, 54.6 x 58.1 mm, 8 parts (0 on the bottom side), 31 nets.

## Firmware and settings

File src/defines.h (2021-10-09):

#ifndef DEFINES_H_
#define DEFINES_H_

#include <Arduino.h>
#include "ui_index.h"
#include <LITTLEFS.h>
#include "ui_fixtures.h"

#ifdef WBLINDS_DEBUG
#include "esp32-hal-log.h"
#define WLOG_I(x...) ESP_LOGI(x)
#define WLOG_D(x...) ESP_LOGD(x)
#define WLOG_E(x...) ESP_LOGE(x)
#else
#define WLOG_I(x...)
#define WLOG_D(x...)
#define WLOG_E(x...)
#endif

#ifndef WBLINDS_DEFINE_GLOBAL_VARS
# define WBLINDS_GLOBAL extern
# define _INIT(x)
# define _INIT_N(x)
#else
# define WBLINDS_GLOBAL
# define _INIT(x) = x

#define UNPACK( ... ) __VA_ARGS__
# define _INIT_N(x) UNPACK x
#endif

#define STRINGIFY(X) #X
#define TOSTRING(X) STRINGIFY(X)

#ifndef W_VERSION
#define W_VERSION "0.0.1"
#endif

// Global Variable definitions
WBLINDS_GLOBAL char VERSION[] _INIT(TOSTRING(W_VERSION));

#include <AsyncJson.h>
#include <ArduinoJson.h>


#define WIFI_CONNECTED (WiFi.status() == WL_CONNECTED)
#define WIFI_CONFIGURED (strlen(wifiSSID) >= 1 && strcmp(wifiSSID, DEFAULT_SSID) != 0)

// DEFAULTS

// Wifi
#define DEFAULT_SSID "WBlinds"

// Pin config defaults
#define DEFAULT_DIR_PIN 17
#define DEFAULT_STEP_PIN 5
#define DEFAULT_SLP_PIN 18
#define DEFAULT_EN_PIN 23
#define DEFAULT_RST_PIN 19
#define DEFAULT_MS1_PIN 1
#define DEFAULT_MS2_PIN 3
#define DEFAULT_MS3_PIN 21
#define DEFAULT_HOME_SWITCH_PIN 4 // microswitch pin for homing

// Dimensions
#define DEFAULT_STEPS_PER_REV 200
#define DEFAULT_CORD_LENGTH_MM 1650
#define DEFAULT_CORD_DIAMETER_MM 0.1
#define DEFAULT_AXIS_DIAMETER_MM 15

// Limits
#define MAX_SSID_LENGTH 32
#define MAX_PW_LENGTH 64
#define MAX_DEVICE_NAME_LENGTH 64
#define MAX_MDNS_NAME_LENGTH 64
#define MAX_MQTT_HOST_LENGTH 128
#define MAX_MQTT_TOPIC_LENGTH 128
#define MAX_MQTT_USER_LENGTH 41
#define MAX_MQTT_PASS_LENGTH 41

// Potentially useful publics
namespace stdBlinds {
    enum class resolution_t {
        kFull = 1,
        kHalf = 2,
        kQuarter = 4,
        kEighth = 8,
        kSixteenth = 16
    };

    enum class error_code_t {
        NoError = 0,
        InvalidJson = 1,
        MissingOp = 2,
        UnknownOp = 3,
        MissingPos = 4
    };

    extern std::map<error_code_t, const char*> ErrorMessage;

    extern const char* MT_JSON;
    extern const char* MT_JPG;
    extern const char* MT_HTML;
}

// ESP
extern uint32_t lastHeap;

// UDP
extern const byte MAGIC_NUMBER[4];

// Access point
extern char apSSID[MAX_SSID_LENGTH];
extern char apPass[MAX_PW_LENGTH];
extern int apChannel;
extern bool apHide;

// Device
extern char deviceName[MAX_DEVICE_NAME_LENGTH];
extern char mDnsName[MAX_MDNS_NAME_LENGTH];

// Wifi
extern bool wifiConfigured;
extern char wifiSSID[MAX_SSID_LENGTH];
extern char wifiPass[MAX_PW_LENGTH];
extern String macAddress;
extern String ipAddress;

// Controls
extern bool lowHeap;
extern bool doReboot;
extern bool doRestore;
extern void DO_REBOOT();
extern void DO_RESTORE();


void uniqueTag(char* out, size_t maxLen, const char* tag);

#endif // DEFINES_H_

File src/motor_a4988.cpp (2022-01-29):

#include "motor_a4988.h"

MotorA4988::MotorA4988() {
  WLOG_I(TAG);

  isInit_ = false;
  auto state = State::getInstance();

  this->axisDiameter_mm_ = state->getAxisDiameter();
  this->cordDiameter_mm_ = state->getCordDiameter();
  this->cordLength_mm_ = state->getCordLength();
  this->stepsPerRev_ = state->getStepsPerRev();
  this->maxTurns_ = calculateMaxTurns((double)axisDiameter_mm_, cordDiameter_mm_, (double)cordLength_mm_);
  setResolution(state->getResolution());
  if(state->isCalibrated()) setMaximumPosition(state->getMaxPosition());

  pinMode(state->getMs1Pin(), OUTPUT);
  pinMode(state->getMs2Pin(), OUTPUT);
  pinMode(state->getMs3Pin(), OUTPUT);
  pinMode(state->getSleepPin(), OUTPUT);
  pinMode(state->getResetPin(), OUTPUT);
  pinMode(state->getEnablePin(), OUTPUT);

  // Not reset
  digitalWrite(state->getResetPin(), HIGH);

  // Not asleep
  isAsleep_ = false;
  digitalWrite(state->getSleepPin(), HIGH);

  // Using auto enable, initially disabled
  isEnabled_ = false;
  digitalWrite(state->getEnablePin(), HIGH);
}

bool MotorA4988::handleTick_(const WBlindsEvent& event) {
  if (!event.flags_.tick_) return false;
  if (!stepper_->isMotorRunning() && !justMoved_) return true;

  auto state = State::getInstance();
  // convert steps to pct
  auto cPos = state->getPosition();
  auto pct = this->getCurrentPercent();
  if (cPos != pct) {
    WLOG_D(TAG, "set current pos: %i", pct);
    state->setPosition(this, pct);
  }

  if(stepper_->isMotorRunning() && !justMoved_) {
    justMoved_ = true;
  } else {
    justMoved_ = false;
  }
  return true;
}

bool MotorA4988::handleMoveEvt_(const WBlindsEvent& event) {
  EventFlags interesting;
  interesting.moveStop_ = true;
  interesting.moveDown_ = true;
  interesting.moveUp_ = true;
  interesting.moveDown_ = true;
  interesting.moveBySteps_ = true;

  if (0 == (interesting.mask_ & event.flags_.mask_)) return false;
  WLOG_I(TAG, "handle move event...");

  if (event.flags_.moveStop_) {
    this->stop(true);
    return true;
  }
  if (event.flags_.moveDown_) {
    this->runDown();
    return true;
  }
  if (event.flags_.moveUp_) {
    this->runDown();
    return true;
  }
  if (event.flags_.moveUp_) {
    this->runDown();
    return true;
  }

  if (event.data_ == nullptr || event.data_->calibData == nullptr) return false;
  if (event.flags_.moveBySteps_) {
    int currPos = this->stepper_->getCurrentPosition();
    WLOG_D(TAG, "moveEvt calib data %i", event.data_->calibData->moveBySteps);

    int32_t newPos = currPos + event.data_->calibData->moveBySteps;
    WLOG_D(TAG, "moveEvt move from %i to: %i", currPos, newPos);
    this->moveTo(newPos);
    return true;
  }

  return false;
}

void MotorA4988::handleEvent(const WBlindsEvent& event) {
  if (handleTick_(event)) return;
  if (handleMoveEvt_(event)) return;

  WLOG_I(TAG, "event mask: %i", event.flags_.mask_);

  auto state = State::getInstance();
  if (event.flags_.atHome_) {
    WLOG_I(TAG, "handle at home event");
    return this->setCurrentPositionAsHome();
  }
  if (event.flags_.atFullyClosed_) {
    WLOG_I(TAG, "handle at closed event");
    int cPos = stepper_->getCurrentPosition();
    setMaximumPosition(cPos);
    state->setMaxPosition(cPos);
    state->setCalibrated(true);
    state->setTargetPosition(100);
    // return this->setCurrentPositionAsHome();
    return;
  }

  if (event.flags_.resolution_) {
    auto resolution = state->getResolution();
    if (this->stepper_->isMotorRunning()) {
      this->stepper_->stopMove();
    }

    WLOG_D(TAG, "new resolution: %i", resolution);
    this->setResolution(resolution);
  }

  bool stoppedMotor = false;
  if (event.flags_.speed_ || event.flags_.accel_) {
    auto speed = state->getSpeed();
    auto accel = state->getAccel();

    if (this->stepper_->isMotorRunning()) {
      stepper_->setDelayToDisable(UINT16_MAX);
      stoppedMotor = true; // restart after
      this->stepper_->stopMove();
    }
    WLOG_D(TAG, "new speed: %i", speed);
    this->setSpeed(speed);
    WLOG_D(TAG, "new accel: %i", accel);
    this->setAccel(accel);
  }
  if (event.flags_.targetPos_ || stoppedMotor) {
    auto tPos = state->getTargetPosition();

    WLOG_D(TAG, "move to target pos: %i", tPos);
    this->moveToPercent(tPos);
    stepper_->setDelayToDisable(DEFAULT_DELAY_TO_DISABLE);

  }
}

// MotorA4988::~MotorA4988() {
//   State::getInstance()->Detach(this);
// }

/**
 * @brief Initialize the motor with an existing engine.
 *
 * @param engine
 */
void MotorA4988::init(FastAccelStepperEngine& engine) {
  auto state = State::getInstance();

  this->engine_ = engine;

  WLOG_D(TAG, "PIN step: %i", state->getStepPin());
  WLOG_D(TAG, "PIN dir: %i", state->getDirectionPin());
  WLOG_D(TAG, "PIN enable: %i", state->getEnablePin());
  WLOG_D(TAG, "PIN ms1: %i", state->getMs1Pin());
  WLOG_D(TAG, "PIN ms2: %i", state->getMs2Pin());
  WLOG_D(TAG, "PIN ms3: %i", state->getMs3Pin());
  WLOG_D(TAG, "PIN reset: %i", state->getResetPin());
  WLOG_D(TAG, "PIN sleep: %i", state->getSleepPin());

  stepper_ = this->engine_.stepperConnectToPin(state->getStepPin());

  stepper_->setDirectionPin(state->getDirectionPin());
  stepper_->setEnablePin(state->getEnablePin());
  // stepper_->disableOutputs();
  stepper_->enableOutputs();
  this->invertDirection();
  stepper_->setAutoEnable(true);
  stepper_->setDelayToDisable(DEFAULT_DELAY_TO_DISABLE);

  // restore state
  int steps = percentToSteps(state->getPosition(), stepsPerPct_, maxPosition_);
  stepper_->setCurrentPosition(steps);
  stepper_->setSpeedInHz(state->getSpeed());
  stepper_->setAcceleration(state->getAccel());

  EventFlags flags;
  flags.pos_ = true;
  flags.speed_ = true;
  flags.resolution_ = true;
  flags.accel_ = true;
  flags.targetPos_ = true;
  flags.moveDown_ = true;
  flags.moveUp_ = true;
  flags.moveStop_ = true;
  flags.tick_ = true;

  // calibration
  flags.atHome_ = true;
  flags.atFullyClosed_ = true;
  flags.moveBySteps_ = true;

  state->Attach(this, flags);

  isInit_ = true;
}

/**
 * @brief Initialize the motor.
 */
void MotorA4988::init() {
  WLOG_I(TAG);

  this->engine_ = FastAccelStepperEngine();
  engine_.init();
  init(engine_);
}

/**
 * @brief Whether the motor/engine is initialized already.
 */
bool MotorA4988::isInit() {
  return isInit_;
}

/**
 * @brief Whether the motor is asleep.
 */
bool MotorA4988::isAsleep() {
  return isAsleep_;
}

/**
 * @brief Whether the motor is enabled.
 */
bool MotorA4988::isEnabled() {
  return isEnabled_;
}
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

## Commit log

2021-06-13 add stls
    [axis-segment-v3.stl, axis-v7.stl, ikea-hoppvals-bearing-mount-v5.stl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]
2021-06-15 new partition, tweaks
    [ESP32_1.7MB_OTA.csv]
2021-06-28 towards calibration flow
2021-06-29 ws and calibration work
2021-06-29 loading button
2021-07-01 before adding calibration events
2021-07-03 add readme section for choosing motor
2021-07-11 calibration working
2021-10-09 update readme, add devkit, new stls
    [axis-segment-v3.stl, axis-v7.stl, base-v5.stl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]
2021-10-09 rotate schematic
2022-01-29 3d screenshots, style tweaks, disable power by default

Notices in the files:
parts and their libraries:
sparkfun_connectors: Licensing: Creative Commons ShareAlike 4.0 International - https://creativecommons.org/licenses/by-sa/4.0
